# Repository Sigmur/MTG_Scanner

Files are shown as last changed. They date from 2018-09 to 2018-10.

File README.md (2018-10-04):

# MTG_Scanner
Magic The gathering card scanning & sorting machine

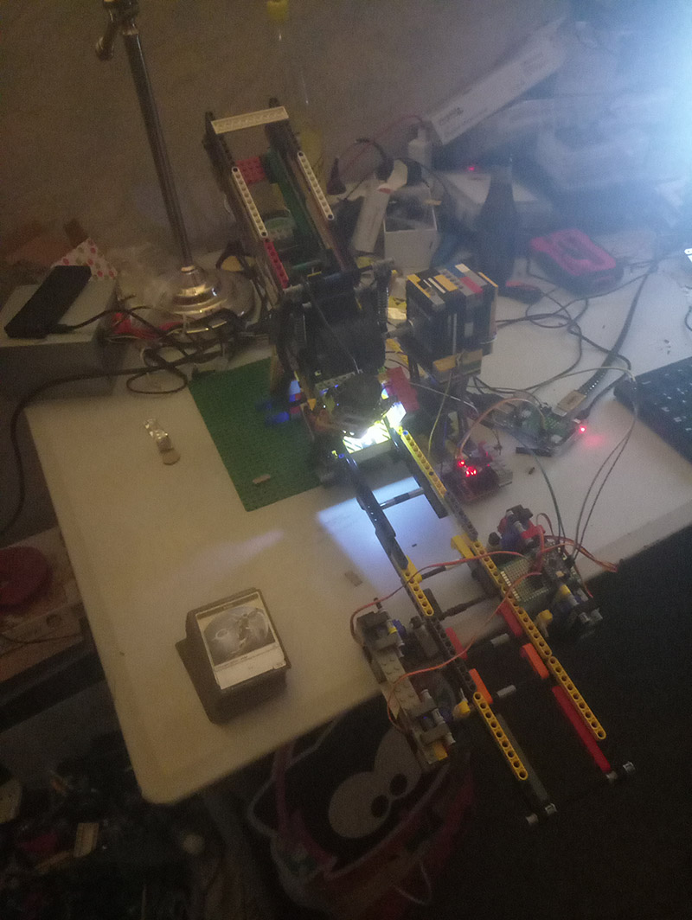
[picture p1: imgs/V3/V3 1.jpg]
Current


Current rev : 3
 - Read cards
 - Open correct filters
 - ~2sec per card
 - Store results in json file for later referencement
 
This is based on the card reference ad the bottom of the card, references were introduced in 2015, so this is not ideal for old cards, but whatever, it'll do for now.
Rev 4 will read card title and do more, but that means getting whole card database from MTG, ect ect. Bleh.

## How it works
  - Hardware side, the machine roll a card from the card dispenser, takes a picture with the camera, software magic happen to read the card, then open the corresponding filter and drop the card in the right bin.
  - Software side, we use OpenCV to cleanup & threshold the image, then send it to Tesseract OCR that will give us a text string from an image, after that the software parse the string using some regexps and voila, we have the card number, extention, language and type.
  
## Why ?
  We bough 15.000 cards from a guy in a garage sale. After an hour of sorting & referencing ~1000 i got bored. So i spent the next month building something to do it automatically. I am not a smart man.
  Edit : we bought another 20k+ cards. Cards, cards everywhere.
  
## Software versions & requirements

### Python 3.4
  
| Name  | Description |
| --- | --- |
| Pillow  | Image manipulation library, required for pytesseract. |
| pytesseract  | Wrapper around Tesseract OCR, see https://pypi.org/project/pytesseract/#installation for more installation instructions |
| mtgsdk  | Will use later, wrapper for easy calls on MTG official API to get card datas  |
| opencv-contrib-python | OpenCV (cv2) is a huge and powerfull image manipulation library, but it's hard to setup on raspberry. I followed http://www.life2coding.com/install-opencv-3-4-0-python-3-raspberry-pi-3/ and had a few problems but got it working in the end  |

  Various required packages for tesseract, opencv, ect ect
  - sudo apt-get install libjpeg8-dev
  - sudo apt-get install libhdf5-dev
  - sudo apt-get install libhdf5-serial-dev
  - sudo apt install libqtgui4
  - sudo apt-get install tesseract-ocr
  
### Arduino

To speed up input/output :
https://github.com/mmarchetti/DirectIO

## Parts used

| Name | Description & usage | Image |
| --- | --- | --- |
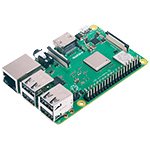
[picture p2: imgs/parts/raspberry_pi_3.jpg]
Raspberry
| Raspberry 3 B+ (1) | The brain of the operation, ~30€ |  |
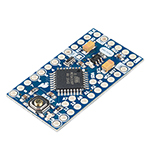
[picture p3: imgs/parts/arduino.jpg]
Arduino pro mini
| Arduino pro mini (~3/4+) | Used to drive the servos. A servo need a PWM signal, this type of arduino has 6 PWM pins, so 6 servos max per arduinos. They can be linked to handle 16/32/64 ... servos. |  |
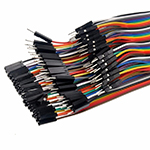
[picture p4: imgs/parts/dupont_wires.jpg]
Dupont wires
| Dupont wires (a LOT) | Buy a lot of them and watch them spread all around your workbench. |  |
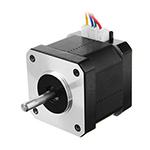
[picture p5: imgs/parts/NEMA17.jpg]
Stepper motor NEMA 17
| Stepper motor Nema 17 40Ncm (1) | Much torque, such precision (1.8°), very power (1.7A). Wow. Commonly found in cheap ass 3d printers (~10€/u). |  |
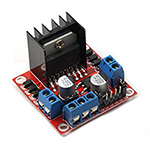
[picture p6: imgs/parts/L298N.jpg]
L298N Stepper driver board
| Stepper motor driver board L298N (1) | Required, or no vroom. ~5€/u |  |
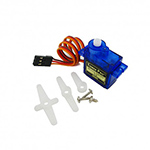
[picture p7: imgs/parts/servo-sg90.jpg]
Servomotor SG90
| Small servomotor SG90 (10+) | Used to move the filters, linked to the arduinos. ~2€/u |  |
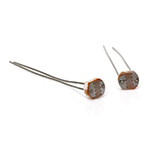
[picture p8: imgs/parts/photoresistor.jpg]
| Photo sensor (1) | Used to detect if a card is right under the camera |  |
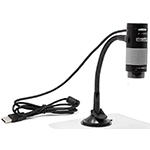
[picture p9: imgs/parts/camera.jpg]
USB camera
| USB Camera 'microscope' (1) | Not realy a microscope, ok magnification, manual calibration, with built in lighting. ~30€. |  |
| Lego (1 fuckton) | I don't have a CNC, but i've gathered the whole family Lego fortune. | - |
| Weird power supply (1) | I reconverted an old computer power supply, thank to our friendly german Great Scott for that trick. It's probably unsafe but heh. | - |

Overall cost ~150€

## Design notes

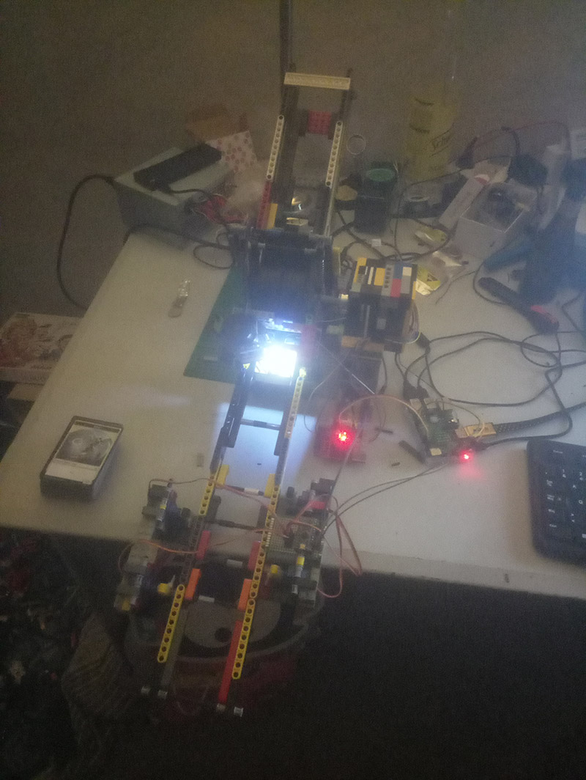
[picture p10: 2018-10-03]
imgs/V3/V3 3.jpg

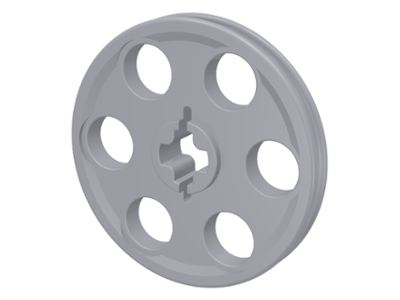
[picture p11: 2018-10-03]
imgs/lego/small_wheel.png

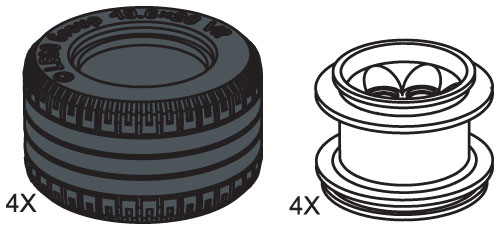
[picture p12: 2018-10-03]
imgs/lego/tires.jpg

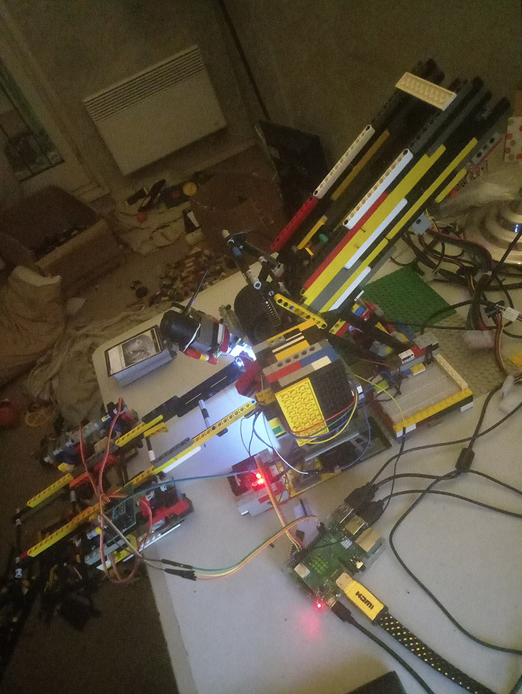
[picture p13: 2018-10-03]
imgs/V3/V3 2.jpg

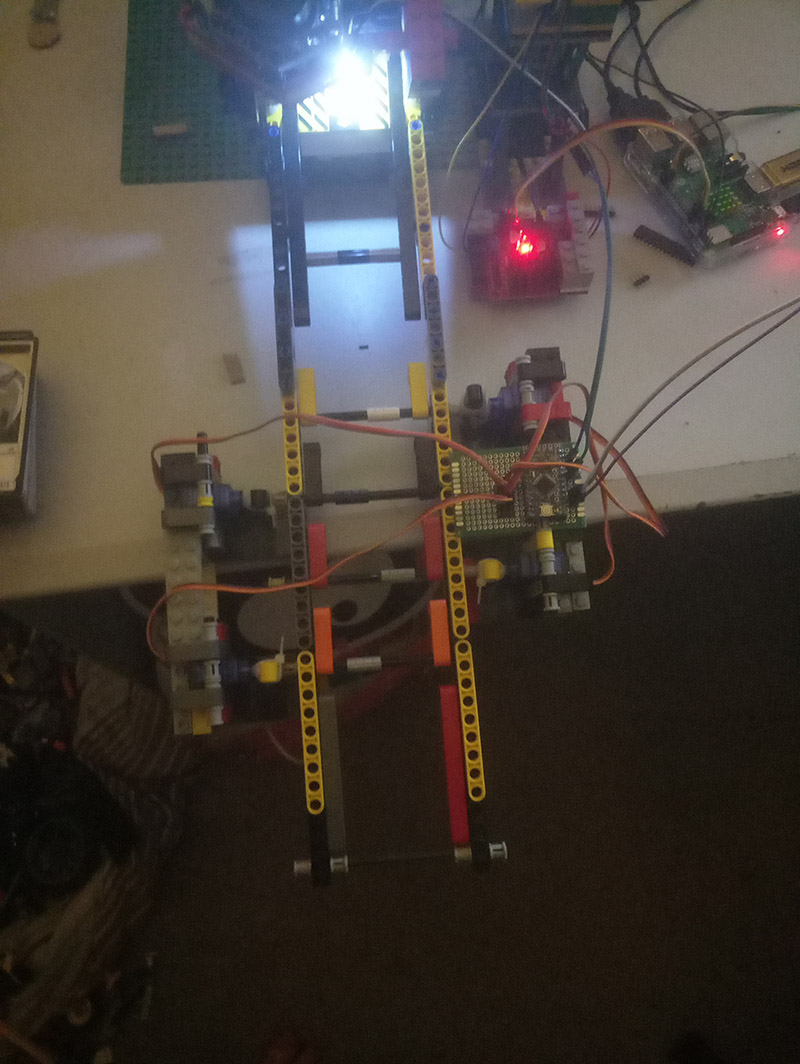
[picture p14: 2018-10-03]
imgs/V3/V3 New filter.jpg

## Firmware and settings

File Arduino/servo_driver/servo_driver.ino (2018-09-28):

/**
 * MIT License
 * 
 * Copyright (c) 2018 Sigmur
 * 
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
 * THE SOFTWARE IS PROVIDED "AS IS", WITHOUT WARRANTY OF ANY KIND, EXPRESS OR
 * IMPLIED, INCLUDING BUT NOT LIMITED TO THE WARRANTIES OF MERCHANTABILITY,
 * FITNESS FOR A PARTICULAR PURPOSE AND NONINFRINGEMENT. IN NO EVENT SHALL THE
 * AUTHORS OR COPYRIGHT HOLDERS BE LIABLE FOR ANY CLAIM, DAMAGES OR OTHER
 * LIABILITY, WHETHER IN AN ACTION OF CONTRACT, TORT OR OTHERWISE, ARISING FROM,
 * OUT OF OR IN CONNECTION WITH THE SOFTWARE OR THE USE OR OTHER DEALINGS IN THE
 * SOFTWARE.
**/

/*
* ------------------------------------------------
* 28/09/2018 - servo_driver.ino
* ------------------------------------------------
* External libaries :
* DirectIO - https://github.com/mmarchetti/DirectIO
* ------------------------------------------------
* - Setup arduino as a servomotor handler on its 6 PWM pins (3, 5, 6, 9, 10, 11)
* - For the machine, we need servos just to open/close filters & drop a card, so no rotation data is required
* - To open/close a servo, send a 16bit integer on pin 0 using pin 1 as clock
* - For each active bit, it will open a servo at the corresponding position
* - If more than 6 bits are up uppon reception, the arduino will shift the 6 used bits and send rest to next arduino
* ------------------------------------------------
* - Ex : Receiving 10154
*      - 0010 0111 1010 1010 => binary form
*	   - On this arduino, use 6 first bits : 0010 01
*	   - Open servos at index 3 and 5 (4th and 6th servos)
*      - Shift number to remove those datas : 
*      - 0010 0111 1010 1010 => 1110 1010 1000 0000
*      - Send new number to next arduino
* ------------------------------------------------
*/

#include <DirectIO.h>
#include <Servo.h>

#define ANGLE_CLOSE			0	//Closed at 0° rotation
#define ANGLE_OPEN			60	//Open at 60° rotation
#define SERVO_PIN_1			3
#define SERVO_PIN_2			5
#define SERVO_PIN_3			6
#define SERVO_PIN_4			9
#define SERVO_PIN_5			10
#define SERVO_PIN_6			11

/* Transmission & reception :
	Transmission :
		Begin, get first bit of int16 to send
		Rise/Drop TX, to fit the bit
		Rise clock
		Wait X ms, benchmark to find good value
		Drop clock
		Repeat TRANSMISSION_SIZE - 1 times with next bits
	Reception :
		Begin, no transmission, clock = LOW
		Clock is rising : start reading transmission
			Read RX
		Clock is dropping, wait for next rise
		Clock is rising again and will do TRANSMISSION_SIZE - 1 times
		On each rise, read RX
*/

#define TRANSMISSION_SIZE	16	//16 bit, max 16 servos
#define CLOCK_DELAY			5	//5 ms (TBD)

#define PIN_RX_CLOCK		1	//Reception clock
#define PIN_RX				0	//Reception pin
#define PIN_TX_CLOCK		13	//Transmission clock
#define PIN_TX				12	//Transmission pin

const int servo_angles[2] = {ANGLE_CLOSE, ANGLE_OPEN};
const int servo_pins[6] = {SERVO_PIN_1, SERVO_PIN_2, SERVO_PIN_3, SERVO_PIN_4, SERVO_PIN_5, SERVO_PIN_6};
Servo servos[6];

//Transmission & reception datas
Input<PIN_RX_CLOCK> reception_clock;
Input<PIN_RX> reception;
Output<PIN_TX_CLOCK> transmission_clock;
Output<PIN_TX> transmission;

bool last_state = false;
int8_t reception_index = 0;
int16_t reception_data = 0;

//--------------------------------------------
// Servo update
//--------------------------------------------

void updateServos(int16_t states)
{
	for (int8_t i = 0; i < 6; i++)
		servos[i].write(servo_angles[(states & (1 << 0))];
}

//--------------------------------------------
// I/O
//--------------------------------------------

void send(int16_t data)
{
	if (transmission_clock != LOW)
		return ;
	
	for (int8_t i = 0; i < TRANSMISSION_SIZE; i++)
	{
		transmission = ((data & (1 << i)) == 0) ? LOW : HIGH; //Transmit 1 if current bit is high, 0 if not
		transmission_clock = HIGH; //Set clock to high
		delay(CLOCK_DELAY); //Wait a bit for other side to read data
		transmission_clock = LOW; //Drop the clock for next transmission
	}
}

void listen()
{
	if (last_state == reception_clock || reception_index >= TRANSMISSION_SIZE)
		return ; //Nothing to do

	if (last_state == LOW && reception_clock == HIGH) //New data to read
		reception_data |= 1UL << reception_index++;
	
	last_state = reception_clock; //Update
}

//--------------------------------------------
// Main
//--------------------------------------------

void setup()
{
	//Init servos
	for (int8_t i = 0; i < 6; i++)
	{
		servos[i].attach(servo_pins[i]);
		servos[i].write(ANGLE_CLOSE);
	}
}

void loop()
{
	if (reception_index == TRANSMISSION_SIZE)
	{ //Just finished a reception, can use reception_data to toggle servos
		updateServos(reception_data); //Toggle servos
		if (reception_data >= 64) //Bit 7 active, send to next arduino
			send(reception_data >> 6); //Move 6 bits to the right, 64 become 1 so servo 7 is first of next board
			//https://www.arduino.cc/reference/en/language/structure/bitwise-operators/bitshiftright/
		//Reset reception
		reception_index = 0;
		reception_data = 0;
	}
	
	listen();
}

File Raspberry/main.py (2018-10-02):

#!/usr/bin/python
'''
MIT License

Copyright (c) 2018 Sigmur

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
THE SOFTWARE IS PROVIDED "AS IS", WITHOUT WARRANTY OF ANY KIND, EXPRESS OR
IMPLIED, INCLUDING BUT NOT LIMITED TO THE WARRANTIES OF MERCHANTABILITY,
FITNESS FOR A PARTICULAR PURPOSE AND NONINFRINGEMENT. IN NO EVENT SHALL THE
AUTHORS OR COPYRIGHT HOLDERS BE LIABLE FOR ANY CLAIM, DAMAGES OR OTHER
LIABILITY, WHETHER IN AN ACTION OF CONTRACT, TORT OR OTHERWISE, ARISING FROM,
OUT OF OR IN CONNECTION WITH THE SOFTWARE OR THE USE OR OTHER DEALINGS IN THE
SOFTWARE.
'''

#sudo apt-get install libjpeg8-dev
#sudo apt-get install tesseract-ocr
#sudo apt-get install libhdf5-dev
#sudo apt-get update
#sudo apt-get install libhdf5-serial-dev
#sudo apt install libqtgui4

import sys
import time
import RPi.GPIO as GPIO
import json
import io
import os
import timing

#Driver for main stepper motor
#from motor import stepper
#Sensor to correct position for card reading
#import photo_resistor
#Camera driver to read card
#import camera
#Resize, process & prepare image for Tesseract
#import image_processing
#Tesseract OCR image to string
#import ocr_processing
#Parse result Tesseract string
#from mtg import parsing
#MTG api call, disabld for now
#import mtg_card_api
#from  motor import filters

#Pinout					BOARD CORNER HERE
# 3.3V  1 #  # 2  5V
# BCM2  3 #  # 4  5V
# BCM3  5 #  # 6  GND
# BCM4  7 #  # 8  BCM14
# GND   9 #  #10  BCM15
# BCM17 11#  #12  BCM18
# BCM27 13#  #14  GND
# BCM22 15#  #16  BCM23
# 3.3V  17#  #18  BCM24
# BCM10 19#  #20  GND
# BCM9  21#  #22  BCM25
# BCM11 23#  #24  BCM8
# GND   25#  #26  BCM7
# BCM0  27#  #28  BCM1
# BCM5  29#  #30  GND
# BCM6  31#  #32  BCM12
# BCM13 33#  #34  GND
# BCM19 35#  #36  BCM16
# BCM26 37#  #38  BCM20
# GND   39#  #40  BCM21

#Stepper pinout
#A_PLUS  = BCM17
#A_MINUS = BCM22
#B_PLUS  = BCM27
#B_MINUS = BCM23
#Photoresitor
#SIGNAL  = BCM4
#Filters
#CLOCK			= BCM20
#TRANSMISSION	= BCM21

program = None


#1) Load program
if len(sys.argv) > 1:
	if sys.argv[1] == 'camera':
		from programs import camera as program
	elif sys.argv[1] == 'calibrate':
		from programs import calibration as program
	elif sys.argv[1] == 'filter:setup':
		from programs import filters_setup as program
	elif sys.argv[1] == 'filter:list':
		from programs import filters_list as program
	else:
		from programs import scanner as program
else:
	from programs import scanner as program
	
program = program.Handler()

#2) Run program
try:
	while True:
		state = program.update();
		if state == True:
			break;

except KeyboardInterrupt:
	print("\n Closing application")
	
finally:
	pass

#3) Cleanup before stop
program.stop()
GPIO.cleanup()

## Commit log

2018-09-28 Add files via upload
    Add arduino servo manager
2018-09-28 Setup raspberry files
    Setup raspberry files, a lot is missing from current raspberry install, will add later
    [camera.py, filters.py, ocr_processing.py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]
2018-09-28 Setup filter communication for Arduino
2018-09-29 =Setup calibration mode
2018-10-01 Setup camera handling on another thread
2018-10-01 Commit missing file, oops
    [main.py]
2018-10-01 Cleanup the code and fix programs. One step at a time.
    [calibration.py, camera.py, filters.py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]
2018-10-02 Setup config file handling, add angle from calibration to main scanner, fix scanner. It is working !
    [calibration.py, camera.py, config.py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]
2018-10-02 Add image for future wiki page Add fritzing layout for future wiki page Add filter setup & filter list programs Add filter handling
    [layout.fzz]
